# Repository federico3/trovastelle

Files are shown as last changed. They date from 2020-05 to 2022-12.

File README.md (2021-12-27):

# Il Trovastelle

Il Trovastelle punta a oggetti interessanti nel cielo e sulla Terra. Sa dove trovare pianeti, lune, e asteroidi, missioni spaziali e satelliti, galassie e nebulose, e amici vicini e lontani.

Il Trovastelle (https://www.youtube.com/watch?v=bgFfTYJVfwA)

## Come funziona

Il Trovastelle usa un accelerometro, una bussola, un giroscopio, e un orologio molto preciso per sapere dove trovare oggetti nel cielo.

[Ecco un video del Trovastelle dall'accensione alle operazioni.]( https://youtu.be/bmjY_7tN_tI )

## Configurazione

Per iniziare, collega un alimentatore da 12V[^1] con jack da 2.1mm (pin centrale positivo) al Trovastelle, e premi il pulsante di accensione.

### Connetti il Trovastelle a Internet

Il Trovastelle funziona senza alcuna connessione a Internet; tuttavia, con una connessione a Internet, può trovare anche satelliti nel cielo (per esempio, Hubble e la ISS).

Per collegare il Trovastelle a Internet, cerca una connessione WiFi aperta dal nome `comitup-XXX`.

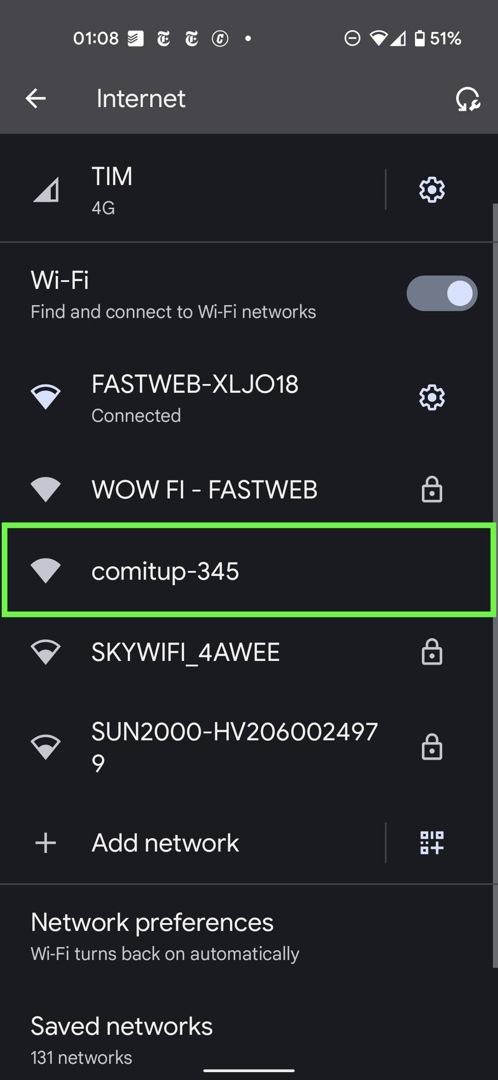
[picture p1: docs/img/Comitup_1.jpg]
Look for an open WiFi network named comitup-XXX


Collegati alla rete WiFi `comitup`. Il tuo computer o telefono aprirà una finestra pop-up che ti chiede di scegliere la tua rete WiFi.

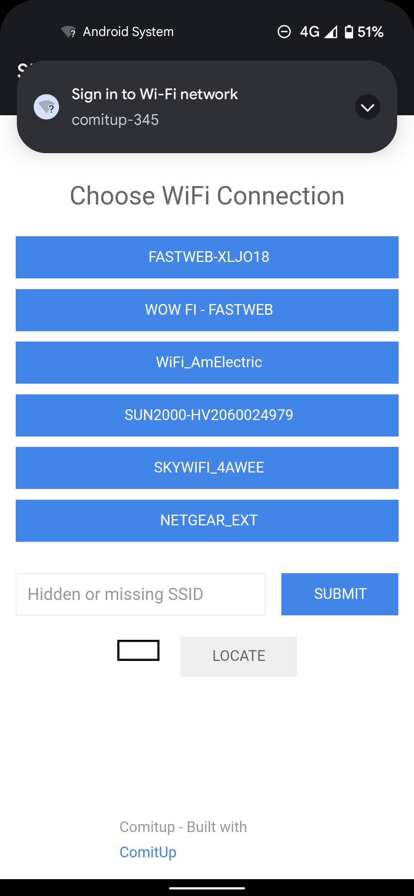
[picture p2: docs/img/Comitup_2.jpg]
Select your WiFi network


Scegli la tua rete WiFi e inserisci la password. Il Trovastelle farà sparire la rete `comitup` e si collegherà al tuo WiFi.

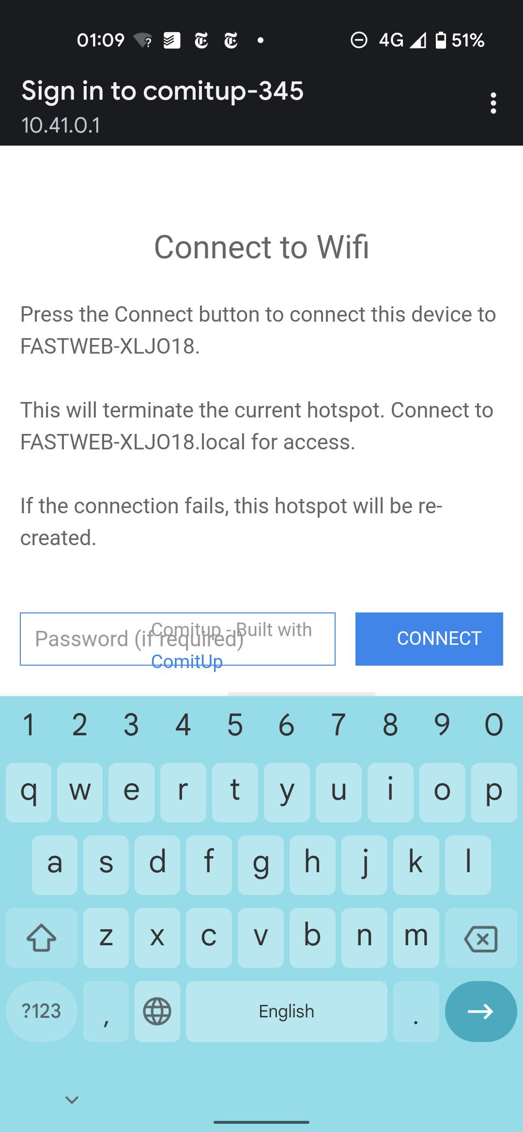
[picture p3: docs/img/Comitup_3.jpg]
Input your WiFi password


### Accedi al Trovastelle

Il cuore del Trovastelle è un computer Raspberry Pi con Linux. Una volta connesso il Trovastelle alla rete WiFi di casa, puoi collegarti al computer via ssh se hai le chiavi giuste:

```
ssh pi@trovastelle1.local
```

Questo comando funzionerà solamente se (i) sei sulla stessa rete WiFi del Trovastelle, e (ii) hai una chiave privata SSH corrispondente alla chiave pubblica caricata sul Trovastelle.

### Telemetria

Il Trovastelle può collegarsi al server di Federico per ricevere aggiornamenti (forse) e aiutare il debug di eventuali problemi. Questa impostazione è disattivata di default. Per attivarla, collegati al Trovastelle via SSH e usa questo comando:
```
sudo systemctl enable autossh
sudo systemctl start autossh
```
Per disattivare questa impostazione, usa questo comando:
```
sudo systemctl stop autossh
sudo systemctl disable autossh
```
Quando la telemetria è attiva, Federico può collegarsi via ssh al Trovastelle, cambiare il programma caricato a bordo, vedere le misure prese dall'accelerometro, giroscopio, e bussola, e comandare i motori, il display, e il LED.

### Progetto meccanico

Il progetto Fusion 360 è [qui](https://a360.co/3moek6k).

[^1]: I motori hanno un voltaggio nominale di 9 e 12V, e dovrebbero funzionare con qualunque voltaggio tra 9 e 18V. Il computer di bordo tollera tra 6 e 21V. Le prove sono state fatte solo a 12V.
  Il Trovastelle non consuma molto: 1A a 12V dovrebbe essere ben più che sufficiente.

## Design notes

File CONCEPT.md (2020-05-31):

# Sky Finder

An arrow that points at interesting objects in the sky, inspired by the art installation at the JPL mall.

## Basic idea

A pointing mechanism (an arrow and/or a laser pointer) that will point out interesting targets in the sky either automatically or in response to user input.

Targets may include

- Stars, galaxies, and other interesting deep sky objects
- Earth satellites
- Locations on Earth (mountains, cities, friends)
- Airplanes?

The mechanism should have a screen to display what is being observed.

## Hardware

### Frame and Assembly

### Motors

Steppers, servos, simple DC motors?

Need a motor driver

### Display

### Laser Pointer

### Brains

System-on-a-chip (SoC) like a Raspberry Pi or microcontroller like ESP/Arduino?

- SoC is way easier to work with (existing astronomy libraries, etc) and has no storage/RAM limitations, but boots slowly and has higher power consumption.
- Microcontroller boots instantly and has lower power usage, but is _very_ limited (a few kBs of RAM).

### Power

USB plug and built-in battery? Need a charge controller to automatically switch from shore power to on-board battery.

## Design concepts

### V1: Sky only, semi-automatic

A pair of stepper motors actuate the pointing mechanism. A microcontroller keeps track of the location of the stepper motors and reports it to SkySafari through the [basic encoder protocol](https://github.com/federico3/DobsonianDSC). [SkySafari](https://play.google.com/store/apps/details?id=com.simulationcurriculum.skysafari5&hl=en_US) issues GOTO commands to the microcontroller via the same protocol. All projections and translations from steps to sky coordinates are performed by Sky Safari.

> TODO: does SkySafari send GoTo commands with the basic protocol?

No screen, no laser pointer, no way to automatically point at objects, calibration needed before every use.

Downside: needs external calibration before use.

### V2: self-calibrating

A compass and accelerometer are installed on the pointing mechanism. This way, the arrow knows where it is pointed (to a precision of a few degrees) in the local alt-az frame. The arrow can communicate its azm-alt to Sky Safari using the [NexStar serial protocol](https://s3.amazonaws.com/celestron-site-support-files/support_files/1154108406_nexstarcommprot.pdf). Conversions from ra-dec to alt-az can be handled with, e.g., [astropy](https://gist.github.com/dokeeffe/18857db66dbabc14679c20a8560e2cd6). 

#### Software updates

- SkySafari compatibility with new protocol
- Cycle through scripted celestial objects autonomously
- Slew to follow satellites autonomously
- Cycle through ground-based objects (lon-lat) autonomously
- Read airplane locations from fr24 or adsbexchange 

#### V2.1: display

V2, but with a display to show what the arrow is pointing at.

#### V2.2: GPS

Automatically get time and location from a GPS receiver.

#### V3.0: laser

V2, but with a laser to point to interesting objects. The laser is controlled by the microcontroller and there is a safety interlock on the base, requiring the user to be present for use.

#### V4.0: camera and astrometry.net

To increase precision, the arrow incorporates a camera that looks at the sky and plate-solves. Probably _very_ unnecessary and may make things more complicated if plate-solving is used by day.

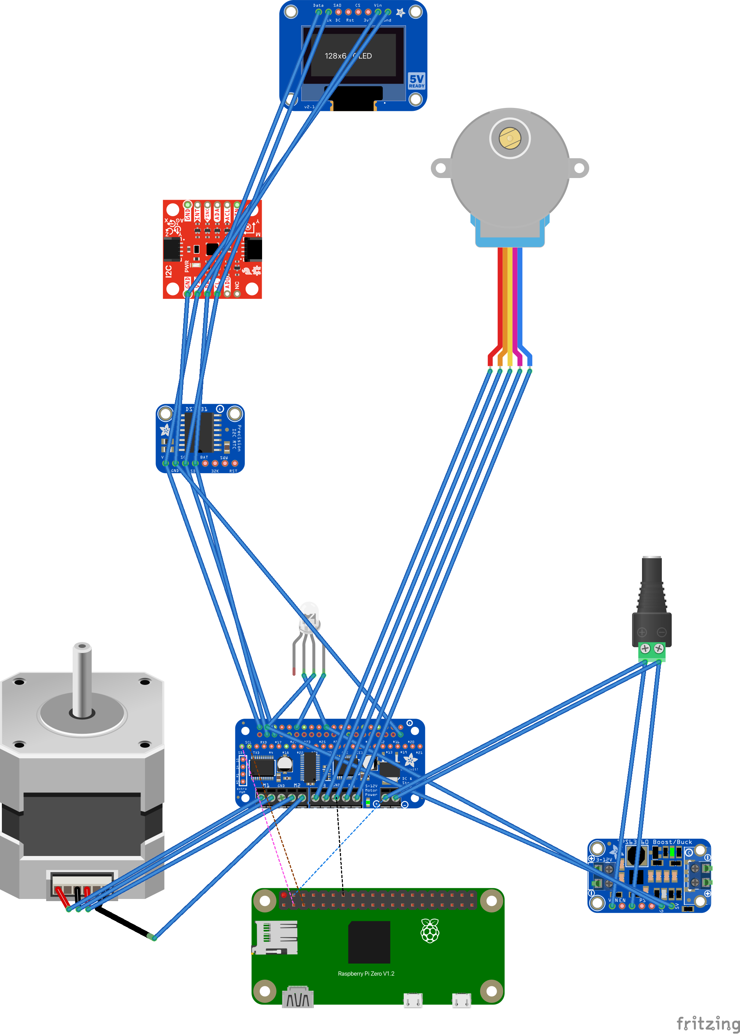
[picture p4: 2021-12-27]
electrical/arrow_bb.png

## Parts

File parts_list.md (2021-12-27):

# Trovastelle

## Hardware

### Computer

- [X] Raspy 0W: $14 https://www.adafruit.com/product/3708

### Motors

- [X] Stepper motors: https://www.adafruit.com/product/858
- [X] https://www.pololu.com/product/1207 16+5

- [X] Motor controller or https://www.adafruit.com/product/4280 (Pi) +22

### Sensors

- [X] Accelerometer+compass: https://www.sparkfun.com/products/15335 $16 or https://www.adafruit.com/product/4646 ($20)

~~GPS: https://www.adafruit.com/product/4415~~

~~QT hat: https://www.adafruit.com/product/4688~~

- [X] RTC https://www.adafruit.com/product/5188 (best) or https://www.adafruit.com/product/5189
- [X] RTC coin cell

### Display

~~Display: https://www.adafruit.com/product/2232 (overkill) or https://www.adafruit.com/product/4567 (monochrome, pretty!) or https://www.adafruit.com/product/2097 (Pi) or https://www.adafruit.com/product/2298 or https://www.aliexpress.com/item/1005003093058462.html~~

- [X] Display: https://www.aliexpress.com/item/1005003093058462.html ($14)

### Other hardware

- [X] Slip ring: https://www.adafruit.com/product/1196 ($20)

- [X] Stepper motor collar: https://www.pololu.com/product/1998 + https://www.pololu.com/product/2693 $7.5+8

- [X] DC barrel: https://www.adafruit.com/product/610 $3

- [X] 12V to 5V buck: https://www.adafruit.com/product/4739 $6

- [X] Power supply: https://www.adafruit.com/product/798 $15

LED may be nice: https://www.sparkfun.com/products/12877 or https://www.sparkfun.com/products/12986

- [X] Power button (AliExpress)

- [X] QWIIC adapter: https://www.adafruit.com/product/4463 or https://www.sparkfun.com/products/15794 or https://www.adafruit.com/product/5142

#### Connectors

- [ ] Connectors: 
  - [X] JST PH connector for motor https://www.adafruit.com/product/5089
  - [X] 2X QWIIC cables https://www.adafruit.com/product/4401
  - [X] 1X QWIIC cable https://www.adafruit.com/product/4399
  - [X] 2X Riser pins https://www.adafruit.com/product/2223
  - [X] Angled riser pins https://www.adafruit.com/product/2823
  - [X] Arcade quick release: https://www.adafruit.com/product/1152
  - [X] Plug jumpers https://www.adafruit.com/product/758
  - [X] Socket jumpers https://www.adafruit.com/product/266
  - [X] Heat shrink https://www.adafruit.com/product/4559

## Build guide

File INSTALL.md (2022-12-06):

# Installation

## Backend

To install the backend, add `trovastelle.service` as a systemd service.

1. Install the Python requirements for Trovastelle with `python -m pip install -r requirements.txt` in the root folder of this repo.
1. Install the package with `python -m pip install -e .` in the root folder of this repo. Note that `-e` symlinks the package to the current folder instead of copying, which is a good idea for development.
1. Ensure that the paths in `trovastelle.service` and `trovastelle.sh` in the `/src/celestial-compass/` folder match the path where this folder is.
1. Copy `trovastelle.service` in the `/src/celestial-compass/` folder to /`etc/systemd/system`.
1. Run `systemctl enable trovastelle`
1. Run `systemctl start trovastelle`

## Frontend

To install the frontend:

1. Copy `trovastelle.wsgi` in the ``/src/celestial-compass/` folder to `/var/www/wsgi-scripts`.
1. Create a file `trovastelle_web.log` in `/var/www/wsgi-scripts` and ensure that it is owned by the `pi` user: `cd /var/www/wsgi-scripts && sudo touch trovastelle_web.log && sudo chown pi trovastelle_web.log`.
1. Compile the frontend with `npm run build` in the `frontend` folder.
1. Copy the frontend installation files in `frontend/build` to `/var/www/frontend`.
1. Ensure that Apache and mod_wsgi are installed.
1. Copy `020-wsgi-backend.conf` to `/etc/apache2/sites-available`. 
1. Run `sudo a2enmod 020-wsgi-backend.conf`.
1. Restart the Apache2 daemon with `sudo systemctl reload apache2`.

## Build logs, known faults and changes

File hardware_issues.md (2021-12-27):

# Problemi hardware

- [ ] Il pin del LED verde è staccato
- [ ] Il riduttore a ingranaggi per l'asse azimuth è rumorosissimo; probabilmente un riduttore a cinghia sarebbe meglio?
- [ ] Il Trovastelle è letteralmente tenuto insieme con lo scotch
- [ ] I cavi sono tenuti in posizione con lo scotch
- [ ] Il magnetometro è molto vicino al motore di elevation, che introduce un sacco di rumore nella misurazione
- [ ] Lo schermo si vede solamente da un lato della freccia
- [ ] Il chip RTC è messo in un posto a caso (con lo scotch) per rendere sufficientemente lungo il cavo che porta segnali alla freccia
- [ ] Le saldature dei cavi sono da software engineer

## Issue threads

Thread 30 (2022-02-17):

Revise Az tracking

federico3, 2022-02-17:
Turns out laser-cut gears are super noisy and inefficient. Consider commercial alternatives.

Also consider making the position of the stepper something we can calibrate.

Options:

- Gears: ~$20
  - [Stepper](https://www.servocity.com/mod-0-8-pitch-pinion-gears/#bore-5mm-round) ($8.5). Can also get more teeth on [eBay](https://www.ebay.com/sch/i.html?_from=R40&_trksid=p2380057.m570.l1313&_nkw=MOD+0.8+5mm&_sacat=0).
  - [Arrow base](https://www.servocity.com/64-tooth-hub-mount-gear-mod-0-8-4mm-thick-acetal/) (number of gears negotiable, $3.5. Can also go aluminum for $10)
  - [Arrow base hub](https://www.servocity.com/1310-series-hyper-hub-8mm-bore/) ($6)
- Timing belts
  - XL $30+8
    - [Stepper](https://www.servocity.com/5mm-15-tooth-pinion-pulley/) $7.6
    - [Arrow base](https://www.servocity.com/timing-hub-pulley/) $6.8
    - [Hub adapter](https://www.servocity.com/1-50-0-770-pattern-adapter/) $4.5
    - [Hub 8mm](https://www.servocity.com/8mm-0-770-clamping-hub/) $6
    - [Belt](https://www.servocity.com/all-xl-series-3-8-width-timing-belts/) $4
  - 3mm ~$26+8
    - [Stepper](https://www.servocity.com/3402-series-3mm-htd-pitch-plastic-hub-mount-timing-belt-pulley-14mm-bore-36-tooth/) $3.4
    - [Stepper hub](https://www.servocity.com/1308-series-lightweight-set-screw-hub-5mm-bore/) $4.7
    - [Arrow base](https://www.servocity.com/3402-series-3mm-htd-pitch-plastic-hub-mount-timing-belt-pulley-14mm-bore-108-tooth/) $6.8
    - [Arrow base hub](https://www.servocity.com/1310-series-hyper-hub-8mm-bore/) ($6)
    - [Timing belt](https://www.servocity.com/3mm-htd-timing-belts/) $5-10
    - [Tensioner bracket](https://www.servocity.com/1524-series-arc-slot-tensioner-bracket/) $5.1
    - [Idler](https://www.servocity.com/acetal-timing-belt-idler-6mm-id-x-12mm-od-18mm-width-1-2-2-pack/) $2.5
- O-ring belt $22+8
  - [Stepper](https://www.servocity.com/3401-series-set-screw-round-belt-pulley-5mm-bore-16mm-pd/) $3.4
  - [Arrow base](https://www.servocity.com/3400-series-hub-mount-round-belt-pulley-14mm-bore-64mm-pd/) $6
  - [Arrow base hub](https://www.servocity.com/1310-series-hyper-hub-8mm-bore/) $6
  - [Tensioner bracket](https://www.servocity.com/1524-series-arc-slot-tensioner-bracket/) $5.1
  - [Idler](https://www.servocity.com/acetal-timing-belt-idler-6mm-id-x-12mm-od-18mm-width-1-2-2-pack/) $2.5 OR [alternative](https://www.servocity.com/1607-series-idler-bearing-6mm-id-x-15mm-od-41mm-length/) $6
  - [Belt](https://www.servocity.com/metric-round-belts-pulleys/#round-belts) $6

A [thinner 8mm hub](https://www.servocity.com/1309-series-sonic-hub-8mm-bore/) (currently sold out).

federico3, 2022-02-17:
Pros and cons.

*Gears*
PRO: cheapest, stiffest.
CON: least efficient, requires precise placement, potentially loud.

*Timing belts*
PROS: more precise than O-ring. Easier to regulate than gears
CON: most expensive, vertical clearance, least reduction (2:1).

*O-ring*
PROS: mid-cost solution, easy to regulate.
CON: potentially slips.

federico3, 2022-04-04:
Progress! https://a360.co/3uOJDeg

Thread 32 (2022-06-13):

Hardware fixes

federico3, 2022-06-13:
- Add a few millimeters to base height
- Move holes for 9DOF a little bit
- Make slightly more room for switch plug and for RPi wiring

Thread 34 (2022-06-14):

Track planes

federico3, 2022-06-14:

federico3, 2022-06-14:
https://openskynetwork.github.io/opensky-api/python.html

federico3, 2022-12-07:
- Build a box around the observer
- Fetch the planes in the box
- Pick the closest one
- Create an Observable that queries the API every 10s and returns lat, lon, alt, similar to Mellyn
- Let skyfiels do the rest
- It the plane is no longer available, pick another one?
- If there are no available planes, delete yourself and call a schedule repair?

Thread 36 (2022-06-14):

Relax calibration

federico3, 2022-06-14:
Adafruit says that, so long as the system calibration level is 1 or higher, we will have North. We can perhaps relax this check to system calibration>=1, or >=2.

https://github.com/federico3/trovastelle/blob/728f7747b047c4d5ffe4e4ecb46975634a518b4d/src/celestial_compass/arrow_controller.py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

federico3, 2022-06-14:
```print(bno055.calibration_status)  #Tuple containing sys, gyro, accel, and mag calibration data```
Just check that sys>=2, or that all are >=2.

federico3, 2022-10-30:
Resolved in #40

Closed 2022-10-30.

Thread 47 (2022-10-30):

Allow user to manually commit updates.

federico3, 2022-10-30:
Right now any update automatically reflects in the application. This also causes the config to get overwritten whenever the page is opened, which is less than great. Fix: add a button to upload configuration, remove autoupload.

Closed 2022-12-04.

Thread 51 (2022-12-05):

Intermittent i2c error in trovastelle2

federico3, 2022-12-05:
Often, trovastelle2 will give this error:

```
➜ python trovastelle.py
Traceback (most recent call last):
  File "/home/pi/trovastelle/src/celestial_compass/trovastelle.py", line 438, in <module>
    asyncio.run(ts.run(),debug=_debug)
  File "/usr/lib/python3.9/asyncio/runners.py", line 44, in run
    return loop.run_until_complete(main)
  File "/usr/lib/python3.9/asyncio/base_events.py", line 642, in run_until_complete
    return future.result()
  File "/home/pi/trovastelle/src/celestial_compass/trovastelle.py", line 399, in run
    await cc_task
  File "/home/pi/trovastelle/src/celestial_compass/compass.py", line 168, in run
    await main_task
  File "/home/pi/trovastelle/src/celestial_compass/compass.py", line 233, in _run_main
    self.display_controller.display_observable_data(
  File "/home/pi/trovastelle/src/celestial_compass/display_manager.py", line 241, in display_observable_data
    self._display_text_in_box(
  File "/home/pi/.local/lib/python3.9/site-packages/luma/core/render.py", line 43, in __exit__
    self.device.display(self.image)
  File "/home/pi/.local/lib/python3.9/site-packages/luma/oled/device/__init__.py", line 225, in display
    self.data(list(buf))
  File "/home/pi/.local/lib/python3.9/site-packages/luma/core/device.py", line 55, in data
    self._serial_interface.data(data)
  File "/home/pi/.local/lib/python3.9/site-packages/luma/core/interface/serial.py", line 125, in data
    write(list(data[i:i + block_size]))
  File "/home/pi/.local/lib/python3.9/site-packages/luma/core/interface/serial.py", line 134, in _write_large_block
    self._bus.i2c_rdwr(self._i2c_msg_write(self._addr, [self._data_mode] + data))
  File "/home/pi/.local/lib/python3.9/site-packages/smbus2/smbus2.py", line 658, in i2c_rdwr
    ioctl(self.fd, I2C_RDWR, ioctl_data)
OSError: [Errno 121] Remote I/O error
```

Looks like this is an i2c error. It may have to do with the clock not being properly stretched, or just some issue with how the display is wired (remember that terrible soldering job?), or just noise. When this happens, the whole application crashes and does not restart.

Closed 2022-12-06.

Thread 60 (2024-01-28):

Add a try-catch for display update

federico3, 2024-01-28:
App keeps crashing while updating the display due to a finicky i2c bus. Ok, it's an hardware issue, but it's annoying.

```
Jan 28 11:40:14 trovastelle2 systemd[1]: Started Trovastelle service.
Jan 28 11:43:54 trovastelle2 trovastelle.sh[4122]: Slow display update prop is False
Jan 28 11:43:54 trovastelle2 trovastelle.sh[4122]: Traceback (most recent call last):
Jan 28 11:43:54 trovastelle2 trovastelle.sh[4122]:   File "/home/pi/trovastelle/src/celestial_compass/trovastelle.py", line 451, in <module>
Jan 28 11:43:54 trovastelle2 trovastelle.sh[4122]:     asyncio.run(ts.run(),debug=_debug)
Jan 28 11:43:54 trovastelle2 trovastelle.sh[4122]:   File "/usr/lib/python3.9/asyncio/runners.py", line 44, in run
Jan 28 11:43:54 trovastelle2 trovastelle.sh[4122]:     return loop.run_until_complete(main)
Jan 28 11:43:54 trovastelle2 trovastelle.sh[4122]:   File "/usr/lib/python3.9/asyncio/base_events.py", line 642, in run_until_complete
Jan 28 11:43:54 trovastelle2 trovastelle.sh[4122]:     return future.result()
Jan 28 11:43:54 trovastelle2 trovastelle.sh[4122]:   File "/home/pi/trovastelle/src/celestial_compass/trovastelle.py", line 412, in run
Jan 28 11:43:54 trovastelle2 trovastelle.sh[4122]:     await cc_task
Jan 28 11:43:54 trovastelle2 trovastelle.sh[4122]:   File "/home/pi/trovastelle/src/celestial_compass/compass.py", line 174, in run
Jan 28 11:43:54 trovastelle2 trovastelle.sh[4122]:     await main_task
Jan 28 11:43:54 trovastelle2 trovastelle.sh[4122]:   File "/home/pi/trovastelle/src/celestial_compass/compass.py", line 239, in _run_main
Jan 28 11:43:54 trovastelle2 trovastelle.sh[4122]:     self.display_controller.display_observable_data(
Jan 28 11:43:54 trovastelle2 trovastelle.sh[4122]:   File "/home/pi/trovastelle/src/celestial_compass/display_manager.py", line 269, in display_o>
Jan 28 11:43:54 trovastelle2 trovastelle.sh[4122]:     self._display_text_in_box(
Jan 28 11:43:54 trovastelle2 trovastelle.sh[4122]:   File "/home/pi/.local/lib/python3.9/site-packages/luma/core/render.py", line 43, in __exit__
Jan 28 11:43:54 trovastelle2 trovastelle.sh[4122]:     self.device.display(self.image)
Jan 28 11:43:54 trovastelle2 trovastelle.sh[4122]:   File "/home/pi/.local/lib/python3.9/site-packages/luma/oled/device/__init__.py", line 225, i>
Jan 28 11:43:54 trovastelle2 trovastelle.sh[4122]:     self.data(list(buf))
Jan 28 11:43:54 trovastelle2 trovastelle.sh[4122]:   File "/home/pi/.local/lib/python3.9/site-packages/luma/core/device.py", line 55, in data
Jan 28 11:43:54 trovastelle2 trovastelle.sh[4122]:     self._serial_interface.data(data)
Jan 28 11:43:54 trovastelle2 trovastelle.sh[4122]:   File "/home/pi/.local/lib/python3.9/site-packages/luma/core/interface/serial.py", line 125, >
Jan 28 11:43:54 trovastelle2 trovastelle.sh[4122]:     write(list(data[i:i + block_size]))
Jan 28 11:43:54 trovastelle2 trovastelle.sh[4122]:   File "/home/pi/.local/lib/python3.9/site-packages/luma/core/interface/serial.py", line 134, >
Jan 28 11:43:54 trovastelle2 trovastelle.sh[4122]:     self._bus.i2c_rdwr(self._i2c_msg_write(self._addr, [self._data_mode] + data))
Jan 28 11:43:54 trovastelle2 trovastelle.sh[4122]:   File "/home/pi/.local/lib/python3.9/site-packages/smbus2/smbus2.py", line 658, in i2c_rdwr
Jan 28 11:43:54 trovastelle2 trovastelle.sh[4122]:     ioctl(self.fd, I2C_RDWR, ioctl_data)
Jan 28 11:43:54 trovastelle2 trovastelle.sh[4122]: OSError: [Errno 121] Remote I/O error
```

federico3, 2024-02-03:
Actually we have already done that but OSError is not caught...

federico3, 2024-02-03:
https://www.geeksforgeeks.org/handling-oserror-exception-in-python/

https://stackoverflow.com/questions/63444603/catch-a-specific-oserror-exception-in-python-3

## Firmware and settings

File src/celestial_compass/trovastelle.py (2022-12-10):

"""
 Copyright (C) 2021 Federico Rossi (347N)
 
 This file is part of Trovastelle.
 
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

from turtle import color
from celestial_compass.display_manager import DisplayController, round_number_to_fixed_width, format_distance, test_distance_format
from celestial_compass.visibility_window import VisibilityWindow
import matplotlib.colors as mcolors
from celestial_compass.arrow_controller import ArrowController, sim9dof, simstepper 
import logging


from celestial_compass.compass import CelestialCompass
from celestial_compass.observables import ObserverLLA

import numpy as np
import os, json
import asyncio
import zmq
import zmq.asyncio
from geojson import Feature, Point, LineString


def get_observables(
    satellites: bool=True,
    missions: bool=True,
    planets: bool=True,
    smallbodies: bool=False,
    mellyn: bool=True,
    messiers: bool=True,
):
    # Observables config
    SPICEYPY_AVAILABLE = False
    try:
        import spiceypy as spice
        SPICEYPY_AVAILABLE = True
    except:
        logging.warning("Spiceypy is not available!")

    from celestial_compass.data.satellites import ObservableSatellites
    if SPICEYPY_AVAILABLE:
        from celestial_compass.data.missions import ObservableMissions
    else:
        from celestial_compass.data.missions_base import ObservableMissions
    from celestial_compass.data.planets import ObservablePlanets
    from celestial_compass.data.small_bodies import ObservableSmallBodies
    from celestial_compass.data.mellyn import ObservableMellyn    
    from celestial_compass.data.messier import ObservableMessiers

    Observables = []
    if satellites:
        Observables += ObservableSatellites
    if missions:
        Observables += ObservableMissions
    if planets:
        Observables += ObservablePlanets
    if smallbodies:
        Observables += ObservableSmallBodies
    if mellyn:
        Observables += ObservableMellyn
    if messiers:
        Observables += ObservableMessiers
    
    return Observables

class trovastelle(object):
    def __init__(self, config, color_schema, store_config=lambda x: None):
    # LED config
        self.config = config
        self.color_schema = color_schema
        logging.debug("Configuring LEDs")
        R_LED = config.get("led_pins",{}).get("red",5)
        G_LED = config.get("led_pins",{}).get("green",6)
        B_LED = config.get("led_pins",{}).get("blue",13)
        A_LED = config.get("led_pins",{}).get("alpha",19)
        led_anode_high = config.get("led_pins",{}).get("anode_high", False)
        led_voltage_scale = config.get("led_pins",{}).get("voltage_scale", 1.)

        self.store_config = store_config

        self.strong_colors_by_type = {
            'Mellon': "xkcd:hot green",
            'Messier': "xkcd:bright orange",
            'Mission': "xkcd:bright red",
            'Planet': "xkcd:true blue",
            'Satellite': "xkcd:very light purple",
        }

        # pale_colors_by_type = {
        #     'Mellon': "xkcd:pale",
        #     'Messier': "xkcd:baby green",
        #     'Mission': "xkcd:light periwinkle",
        #     'Planet': "xkcd:pale mauve",
        #     'Satellite': "xkcd:magenta",
        # }

        logging.debug("Configuring display")
        simulated_display = config.get("simulated",{}).get("display",False)
        if simulated_display:
            import luma.emulator.device
            device = luma.emulator.device.capture()
            display_controller = DisplayController(device=device, slow_display_update=config.get("slow_display_update", True))
            logging.info("Using simulated display in trovastelle")
        else:
            display_controller = DisplayController(slow_display_update=config.get("slow_display_update", True))
            logging.info("Using real display in trovastelle")
        display_controller.display_fullscreen_text("Trovastelle")


        logging.debug("Configuring observables")
        Observables = get_observables(
            satellites  = config.get("observables",{}).get("satellites",True),
            missions    = config.get("observables",{}).get("missions",True),
            planets     = config.get("observables",{}).get("planets",True),
            smallbodies = config.get("observables",{}).get("smallbodies",False),
            mellyn      = config.get("observables",{}).get("mellyn",True),
            messiers    = config.get("observables",{}).get("messiers",True),
        )

        logging.debug("Configuring observer")
        # Observer: Marzia
        # _observer = ObservableMellyn[4]

        observer = ObserverLLA(
            lat_rad = config.get("observer",{}).get("lat_deg_N", 34.1376481)*np.pi/180.,
            lon_rad = config.get("observer",{}).get("lon_deg_E",-118.138686)*np.pi/180.,
            alt_m   = config.get("observer",{}).get("alt_m", 204.),
        )

        logging.debug("Configuring arrow controller")
        # Arrow controller
        ac = ArrowController(
            simulate_motors=config.get("simulated",{}).get("motors",False),
            simulate_9dof=config.get("simulated",{}).get("9dof",False),
            steps_per_turn_alt=config.get("steppers",{}).get("steps_per_turn_alt",2052),
            steps_per_turn_az=config.get("steppers",{}).get("steps_per_turn_az",int(200*16/6)),
            az_offset_rad=-np.pi/2, # HORRIBLE HACK! But works on Federico's desk, and YOLO
            alt_direction_up = config.get("steppers",{}).get("alt_direction_up", 2) , # 1 is forward, 2 is backwards
            az_direction_cw = config.get("steppers",{}).get("az_direction_cw", 2) ,
        )

        logging.debug("Configuring Trovastelle")
        # Full controller
        self.cc = CelestialCompass(
                controller= ac,
                observer = observer,
                observables = Observables,
                time_on_target_s = config.get("observables_list",{}).get("time_on_target_s",150.),
                target_list_length_s = config.get("observables_list",{}).get("target_list_length_s",600.),
                check_visible= config.get("observables_list",{}).get("check_visible",False),
                visibility_window = VisibilityWindow(
                    min_alt_rad= config.get("observables_list",{}).get("visibility_window",{}).get("min_alt_rad",-np.pi/2.),
                    max_alt_rad= config.get("observables_list",{}).get("visibility_window",{}).get("max_alt_rad", np.pi/2.),
                    min_az_rad = config.get("observables_list",{}).get("visibility_window",{}).get("min_az_rad",  0.),
                    max_az_rad = config.get("observables_list",{}).get("visibility_window",{}).get("max_az_rad",2*np.pi),
                ),
                refresh_rate_hz=config.get("observables_list",{}).get("refresh_rate_hz",1.),
                display_controller=display_controller,
                simulated_display=config.get("simulated",{}).get("display",False),
                simulated_led=config.get("simulated",{}).get("led",False),
                led_pins_rgba = (R_LED, G_LED, B_LED, A_LED),
                led_anode_high = led_anode_high,
                led_voltage_scale = led_voltage_scale,
                led_colors=color_schema.get(config.get("led_color_scheme","strong"), self.strong_colors_by_type),
                calibration_level=config.get("calibration_level",3),
                slow_display_update=config.get("slow_display_update", True),
            )


    def calibrate(self):
        logging.info("Calibrating! Trovastelle")
    
        self.cc.calibrate()

    async def listen(self):
        """ This is where you put your sockets, etc. """
        """ https://pyzmq.readthedocs.io/en/latest/api/zmq.asyncio.html """
        context = zmq.asyncio.Context()
        sock = context.socket(zmq.REP)
        sock.bind("tcp://*:5556")
        while True:
            msg = await sock.recv() # waits for msg to be ready
            req = msg.decode()
            if len(req) == 2 and req[:2] == "GC":
                logging.debug("Received request for config")
                reply = json.dumps(self.config)

            elif len(req) == 2 and req[:2] == "GA":
                logging.debug("Received request for calibration status")
                reply = json.dumps(self.cc.controller.calibration_status)
            
            elif len(req) == 2 and req[:2] == "GO":
                logging.debug("Received request for observer location status")
                reply = json.dumps({"lat_deg_N": self.cc.observer.lat_rad*180./np.pi, "lon_deg_E": self.cc.observer.lon_rad*180./np.pi, "alt_m": self.cc.observer.alt_m})
            
            elif len(req) == 2 and req[:2] == "GL":
                logging.debug("Received request for list")
                _schedule_json = []
                for scheduled_ix, scheduled in enumerate(self.cc.schedule):
                    _ra_radians_start, _dec_radians_start, _distance = scheduled['observable'].observe_topocentric_ra_dec(
                        observer_lon_E_deg=self.cc.observer.lon_rad*180./np.pi,
                        observer_lat_N_deg=self.cc.observer.lat_rad*180./np.pi,
                        observer_h_m=self.cc.observer.alt_m,
                        observing_time=scheduled['start_time']
                        )
                    _ra_radians_end, _dec_radians_end, _distance = scheduled['observable'].observe_topocentric_ra_dec(
                        observer_lon_E_deg=self.cc.observer.lon_rad*180./np.pi,
                        observer_lat_N_deg=self.cc.observer.lat_rad*180./np.pi,
                        observer_h_m=self.cc.observer.alt_m,
                        observing_time=scheduled['end_time']
                        )
                    # if (_ra_radians_start==_ra_radians_end and _dec_radians_start==_dec_radians_end):
                    if True:
                        _geometry = Point((
                                _ra_radians_start*180/np.pi,
                                _dec_radians_start*180/np.pi
                            ))
                    else:
                        _geometry = LineString([
                            (_ra_radians_start*180/np.pi,_dec_radians_start*180/np.pi),
                            (_ra_radians_end*180/np.pi,  _dec_radians_end*180/np.pi)
                            ])
                    _schedule_json.append(
                        Feature(
                            properties={
                                "name": scheduled['observable'].name,
                                "type": scheduled['observable'].type_name,
                                "order": scheduled_ix, 
                                "start_time": scheduled['start_time'].strftime("%m/%d/%Y, %H:%M:%S"),
                                "end_time": scheduled['end_time'].strftime("%m/%d/%Y, %H:%M:%S"),
                                "color_rgb": scheduled['color_rgb']
                            },
                            geometry= _geometry
                        )
                    )

                reply = json.dumps({"type":"FeatureCollection","features": _schedule_json})
            
            elif len(req) == 2 and req[:2] == "GP":
                logging.debug("Received request for pointer location")
                _alt_rad, _az_rad = self.cc.controller.get_alt_az()
                reply = json.dumps({"alt_rad": _alt_rad, "az_rad": _az_rad})

            elif len(req) >=2 and req[:2] == "SC":
                _config = json.loads(req[2:])
                logging.info("Processing new dictionary!")
                # print(_config)
                # Dynamic update behavior:
                # - Update observer: update cc.observer, set cc.schedule = [], call cc.update_schedule()
                # - Update observables: set cc.schedule = [], call cc.update_schedule()
                # - Update LED pins: requires application reboot
                # - Update LED color scheme: set cc.schedule = [], call cc.update_schedule() (or we could just update the colors one by one)
                # - Update stepper settings: requires application reboot
                # - Update observables_list parameters: 
                #   - update cc.time_on_target_s | target_list_length_s | check_visible | visibility_window,  set cc.schedule = [], call cc.update_schedule()
                #   - update cc.refresh_rate_hz and continue running with existing
                # - Update simulated: requires application reboot
                _update_schedule = False
                _restart = False
                if "observables" in _config.keys() and _config["observables"] != self.config["observables"]:
                    logging.info("New observables")
                    logging.debug("Fetching new observables: {}".format(_config.get("observables",{})))
                    _Observables = get_observables(
                        satellites  = _config.get("observables",{}).get("satellites",True),
                        missions    = _config.get("observables",{}).get("missions",True),
                        planets     = _config.get("observables",{}).get("planets",True),
                        smallbodies = _config.get("observables",{}).get("smallbodies",False),
                        mellyn      = _config.get("observables",{}).get("mellyn",True),
                        messiers    = _config.get("observables",{}).get("messiers",True),
                    )
                    logging.debug("Fetched {} new observables".format(len(_Observables)))
                    # Very weird, this sometimes does not work. Some race condition?
                    _updated_observables = self.cc.update_observables(_Observables)
                    logging.debug("Updated observables: {}".format(_updated_observables))
                    # self.cc.observables = _Observables
                    _update_schedule = True
                    self.config["observables"] = _config["observables"]

                if "observer" in _config.keys() and _config["observer"] != self.config["observer"]:
                    logging.info("New observer")
                    self.cc.observer = ObserverLLA(
                        lat_rad = float(_config.get("observer",{}).get("lat_deg_N", 34.1376481)*np.pi/180.),
                        lon_rad = float(_config.get("observer",{}).get("lon_deg_E",-118.138686)*np.pi/180.),
                        alt_m   = float(_config.get("observer",{}).get("alt_m", 204.)),
                    )
                    _update_schedule = True
                    self.config["observer"] = _config["observer"]

                if "observables_list" in _config.keys() and _config["observables_list"] != self.config["observables_list"]:
                    logging.info("New observable list parameters")
                    self.cc.time_on_target_s = int(_config.get("observables_list",{}).get("time_on_target_s", 150))
                    self.cc.target_list_length_s = int(_config.get("observables_list",{}).get("target_list_length_s", 600))
                    self.cc.check_visible = _config.get("observables_list",{}).get("check_visible", True)
                    self.cc.visibility_window = VisibilityWindow(
                        min_alt_rad= float(_config.get("observables_list",{}).get("visibility_window",{}).get("min_alt_rad",-np.pi/2.)),
                        max_alt_rad= float(_config.get("observables_list",{}).get("visibility_window",{}).get("max_alt_rad", np.pi/2.)),
                        min_az_rad = float(_config.get("observables_list",{}).get("visibility_window",{}).get("min_az_rad",  0.)),
                        max_az_rad = float(_config.get("observables_list",{}).get("visibility_window",{}).get("max_az_rad",2*np.pi)),
                    )
                    self.cc.refresh_rate_hz = _config.get("observables_list",{}).get("refresh_rate_hz", 1.)
                    _update_schedule = True
                    self.config["observables_list"] = _config["observables_list"]

                if "calibration_level" in _config.keys() and _config["calibration_level"] != self.config["calibration_level"]:
                    logging.info("New calibration level - this will really take effect at the next restart")
                    self.cc.calibration_level = _config["calibration_level"] # This line is quite ineffective, actually. The important thing is that the setting gets saved to disk.
                    self.config["calibration_level"] = _config["calibration_level"]

                if "led_color_scheme" in _config.keys() and _config["led_color_scheme"] != self.config["led_color_scheme"]:
                    logging.info("New color scheme")
                    self.cc.led_colors = self.color_schema.get(_config.get("led_color_scheme","strong"), self.strong_colors_by_type),
                    _update_schedule = True
                    self.config["led_color_scheme"] = _config["led_color_scheme"]

                if "led_pins" in  _config.keys() and _config["led_pins"] != self.config["led_pins"]:
                    logging.info("New LED pins")
                    self.config["led_pins"] = _config["led_pins"]
                    _restart = True

                if "steppers" in  _config.keys() and _config["steppers"] != self.config["steppers"]:
                    logging.info("New stepper properties")
                    self.config["steppers"] = _config["steppers"]
                    _restart = True

                if "simulated" in  _config.keys() and _config["simulated"] != self.config["simulated"]:
                    logging.info("New simulation properties")
                    self.config["simulated"] = _config["simulated"]
                    _restart = True

                if "slow_display_update" in  _config.keys() and _config["slow_display_update"] != self.config["slow_display_update"]:
                    logging.info("New slow display update configuration: {}".format(_config["slow_display_update"]))
                    self.cc.display_controller.slow_display_update = _config["slow_display_update"]
                    self.config["slow_display_update"] = _config["slow_display_update"]
                
                # self.config = _config # We do this piecemeal
                # Store configuration on disk!
                self.store_config(self.config)

                if _update_schedule is True:
                    logging.info("Updating schedule")
                    self.cc.schedule = []
                    self.cc.update_schedule()
                if _restart is True:
                    logging.info("Restarting")
                    pass # TODO Raise an Exception or just quit and systemd will respawn us
                reply_code = "OK"
                reply = reply_code+json.dumps(self.config)
            elif len(req) >=2 and req[:2] == "SO":
                _new_observer = json.loads(req[2:])
                if (
                    type(_new_observer) is not dict or
                    "lon_deg_E" not in _new_observer.keys() or
                    "lat_deg_N" not in _new_observer.keys() or
                    "alt_m" not in _new_observer.keys() or
                    np.abs(_new_observer["lon_deg_E"])>180. or
                    np.abs(_new_observer["lat_deg_N"])>90.
                ):
                    logging.warning("New observer is invalid (SO)")
                    reply_code = "NO"
                else:
                    logging.debug("New observer is valid, processing")
                    if (
                        self.cc.observer.lat_rad != _new_observer["lat_deg_N"]*np.pi/180. or
                        self.cc.observer.lon_rad != _new_observer["lon_deg_E"]*np.pi/180. or
                        self.cc.observer.alt_m != _new_observer["alt_m"]
                    ):

                        self.cc.observer = ObserverLLA(
                            lat_rad = _new_observer["lat_deg_N"]*np.pi/180.,
                            lon_rad = _new_observer["lon_deg_E"]*np.pi/180.,
                            alt_m   = _new_observer["alt_m"],
                        )

                        self.config["observer"] = _new_observer
                        self.cc.schedule = []
                        self.cc.update_schedule()
                    else:
                        logging.debug("Observer has not changed")
                    reply_code = "OK"
                    
                # reply = await async_process(msg)
                reply = reply_code+json.dumps(self.config["observer"])

            elif len(req) >=2 and req[:2] == "DL":
                logging.info("Received request to delete and reset schedule list")
                self.cc.schedule = []
                self.cc.update_schedule()
                reply = "OK";
            else:
                reply = "NO";
            await sock.send(reply.encode())

    async def run(self):
        cc_task = asyncio.create_task(self.cc.run())
        io_task = asyncio.create_task(self.listen())
        await cc_task
        await io_task
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

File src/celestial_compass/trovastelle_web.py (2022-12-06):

"""
 Copyright (C) 2021 Federico Rossi (347N)
 
 This file is part of Trovastelle.
 
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
import logging
import os, json
import asyncio
import zmq
import zmq.asyncio
from flask import Flask, request

from flask_cors import CORS



REQUEST_TIMEOUT = 10000
REQUEST_RETRIES = 3
SERVER_ENDPOINT = "tcp://localhost:5556"
DATA_PATH = os.environ.get("CELESTIAL_COMPASS_DATA")

class trovastelle_web_stateless(object):
    def __init__(self, endpoint, timeout, retries):
        self.endpoint = endpoint
        self.timeout = timeout

    def get_configuration(self):
        command = 'GC'
        request = str(command).encode()
        logging.info("Sending (%s)", request)
        context = zmq.Context()
        client = context.socket(zmq.REQ)
        client.connect(self.endpoint)

        client.send(request)
        while True:
            if (client.poll(REQUEST_TIMEOUT) & zmq.POLLIN) != 0:
                reply = client.recv().decode()
                try:
                    config = json.loads(reply)
                    retries_left = REQUEST_RETRIES
                    logging.info("Server replied OK (%s)", reply)
                    return config
                except ValueError:                    
                    logging.error("Malformed reply from server (%s): %s", command[:2], reply)
                    return None

    def get_observer(self):
        command = 'GO'
        request = str(command).encode()
        logging.info("Sending (%s)", request)
        context = zmq.Context()
        client = context.socket(zmq.REQ)
        client.connect(self.endpoint)

        client.send(request)
        while True:
            if (client.poll(REQUEST_TIMEOUT) & zmq.POLLIN) != 0:
                reply = client.recv().decode()
                try:
                    config = json.loads(reply)
                    retries_left = REQUEST_RETRIES
                    logging.info("Server replied OK (%s)", reply)
                    return config
                except ValueError:                    
                    logging.error("Malformed reply from server (%s): %s", command[:2], reply)
                    return None

    def get_list(self):
        command = 'GL'
        request = str(command).encode()
        logging.info("Sending (%s)", request)
        context = zmq.Context()
        client = context.socket(zmq.REQ)
        client.connect(self.endpoint)

        client.send(request)
        while True:
            if (client.poll(REQUEST_TIMEOUT) & zmq.POLLIN) != 0:
                reply = client.recv().decode()
                try:
                    config = json.loads(reply)
                    retries_left = REQUEST_RETRIES
                    logging.info("Server replied OK (%s)", reply)
                    return config
                except ValueError:                    
                    logging.error("Malformed reply from server (%s): %s", command[:2], reply)
                    return None

    def delete_list(self):
        command = 'DL'
        request = str(command).encode()
        logging.info("Sending (%s)", request)
        context = zmq.Context()
        client = context.socket(zmq.REQ)
        client.connect(self.endpoint)

        client.send(request)
        while True:
            if (client.poll(REQUEST_TIMEOUT) & zmq.POLLIN) != 0:
                reply = client.recv().decode()
                if reply[:2] != "OK":
                    logging.warning("Warning: non-OK reply from Trovastelle")
                    return False
                else:
                    return True


    def get_calibration(self):
        command = 'GA'
        request = str(command).encode()
        logging.info("Sending (%s)", request)
        context = zmq.Context()
        client = context.socket(zmq.REQ)
        client.connect(self.endpoint)

        client.send(request)
        while True:
            if (client.poll(REQUEST_TIMEOUT) & zmq.POLLIN) != 0:
                reply = client.recv().decode()
                try:
                    config = json.loads(reply)
                    retries_left = REQUEST_RETRIES
                    logging.info("Server replied OK (%s)", reply)
                    return config
                except ValueError:                    
                    logging.error("Malformed reply from server (%s): %s", command[:2], reply)
                    return None

    def get_altaz(self):
        command = 'GP'
        request = str(command).encode()
        logging.info("Sending (%s)", request)
        context = zmq.Context()
        client = context.socket(zmq.REQ)
        client.connect(self.endpoint)

        client.send(request)
        while True:
            if (client.poll(REQUEST_TIMEOUT) & zmq.POLLIN) != 0:
                reply = client.recv().decode()
                try:
                    config = json.loads(reply)
                    retries_left = REQUEST_RETRIES
                    logging.info("Server replied OK (%s)", reply)
                    return config
                except ValueError:                    
                    logging.error("Malformed reply from server (%s): %s", command[:2], reply)
                    return None

    def set_configuration(self, config):
        command = "SC"+json.dumps(config)
        request = str(command).encode()
        logging.debug("Sending (%s)", request)
        context = zmq.Context()
        client = context.socket(zmq.REQ)
        client.connect(self.endpoint)

        client.send(request)
        while True:
            if (client.poll(REQUEST_TIMEOUT) & zmq.POLLIN) != 0:
                reply = client.recv().decode()
                if reply[:2] != "OK":
                    logging.warning("Warning: non-OK reply from Trovastelle")
                try:
                    logging.warning(reply[2:])
                    config = json.loads(reply[2:])
                    retries_left = REQUEST_RETRIES
                    logging.warning("Server replied (%s)", reply)
                    return config
                    
                except ValueError:                    
                    logging.error("Malformed reply from server (%s): %s", command[:2], reply)
                    continue

    def set_observer(self, config):
        command = "SO"+json.dumps(config)
        request = str(command).encode()
        logging.debug("Sending (%s)", request)
        context = zmq.Context()
        client = context.socket(zmq.REQ)
        client.connect(self.endpoint)
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

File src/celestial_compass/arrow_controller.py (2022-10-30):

"""
 Copyright (C) 2021 Federico Rossi (347N)
 
 This file is part of Trovastelle.
 
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
from celestial_compass.observables import ObserverLLA
import numpy as np
import time
import logging
from scipy.spatial.transform import Rotation

BOARD_AVAILABLE=False
try:
    import board
    import adafruit_bno055
    from adafruit_motorkit import MotorKit

    BOARD_AVAILABLE=True
except NotImplementedError as e:
    logging.warning("Not on hardware!")
    board = None

from adafruit_motor import stepper

import geomag
import math

class sim9dof(object):
    def __init__(self, euler: list=(0,0,0), quaternion: list=(1,0,0,0)):
        self.euler = euler
        self.quaternion = quaternion
        self.calibrated = True
        self.calibration_status = (3,3,3,3)
        
class simstepper(object):
    def __init__(self):
        self._step = 0
    def onestep(
        self,
        direction,
        style,
    ):
        self._step += 1*direction
        return self._step
    def release(self):
        return True

class ArrowController(object):
    """
    """
    def __init__(
        self,
        steps_per_turn_alt:int=2052,
        steps_per_turn_az:int=200,
        observer:ObserverLLA=ObserverLLA(
            lat_rad=45.*np.pi/180.,
            lon_rad=8.*np.pi/180.
        ),
        az_offset_rad: float=0,
        simulate_motors: bool=False,
        simulate_9dof: bool=False,
        alt_direction_up = stepper.BACKWARD,
        az_direction_cw = stepper.BACKWARD,
    ):
        self.alt_rad = None
        self.az_rad = None
        self.az_offset_rad = az_offset_rad
        self.steps_per_turn_alt = steps_per_turn_alt
        self.steps_per_turn_az = steps_per_turn_az
        self.observer = observer
        self.alt_direction_up = alt_direction_up
        self.az_direction_cw = az_direction_cw
        
        if simulate_9dof:
            self.bno055 = sim9dof()
        else:
            i2c = board.I2C()
            self.bno055 = adafruit_bno055.BNO055_I2C(i2c)
        
        if simulate_motors:
            self.stepper_alt = simstepper()
            self.stepper_az = simstepper()
        else:
            self.motorkit = MotorKit()
            self.stepper_alt = self.motorkit.stepper2
            self.stepper_az = self.motorkit.stepper1
        
        self.style_alt = stepper.SINGLE
        self.style_az = stepper.SINGLE
        
        if self.style_az == stepper.MICROSTEP:
            self.steps_per_turn_az *= 16
        if self.style_alt == stepper.MICROSTEP:
            self.steps_per_turn_alt *= 16
        
    def __del__(self):
        try:
            self.stepper_alt.release()
        except:
            logging.error("Could not release alt stepper on exit!")
        try:
            self.stepper_az.release()
        except:
            logging.error("Could not release ax stepper on exit!")
        
    def get_alt_az(self):
        _euler_angles = self.bno055.euler
        # We believe the Euler angles are Z, Y, X, with Z up and Y
        # The order of the Euler angles is RPY. P is alt, Y is az. ???
        # Also note that this is problematic if the base is tilted
        _alt_rad_raw = _euler_angles[1]*np.pi/180.
        _az_rad_raw = _euler_angles[2]*np.pi/180.
        
        # Quaternion is in w, x, y, z format. See table 3-30 in datasheet
        _quaternion = self.bno055.quaternion
        # This wants to be in scalar-last format, see https://docs.scipy.org/doc/scipy/reference/generated/scipy.spatial.transform.Rotation.html
        _rotation = Rotation.from_quat([_quaternion[1], _quaternion[2], _quaternion[3], _quaternion[0]])
        # TODO this is where we figure out the actual axes based on Section 3.4 in the datasheet
        # https://cdn-shop.adafruit.com/datasheets/BST_BNO055_DS000_12.pdf
        # Consider a setup with z axis for az and y axis for alt. Then we want z y x, and we will ignore x.
        # Based on the markings on the chip: https://www.adafruit.com/product/4646
        # This may be Y Z X
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

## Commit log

2021-11-06 Add: LED Manager. Also minor bug fixes
    [led_manager.py]
2021-11-06 Add: local changes on RPi with LED manager sketch
2021-11-07 Add: display manager and debug. Added a display manager for the ssd1309, based on luma library. Note that the i2c speed should be increased, or the display won't work. Also, WOW are SMD parts hard, a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
    [display_manager.py, observables.py]
2021-11-07 Bugfix: clean up display library
    [display_manager.py]
2021-12-06 Fix: handle case where PyEphem is not available
    [observables.py]
2021-12-06 Fix: type incompatibility with Python3.6
    [observables.py]
2021-12-09 Display controller and streamlining. 1. Added new display controller that shows name, type, and distance. 2. Updated Observable type to carry type. 3. Cleaned up Observables to use less memory, reduc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
    [display_manager.py, observables.py]
2021-12-11 Assembling end to end SW
2021-12-12 Add: async LED behavior
2021-12-12 Fix: license. This software was developed by Federico in his spare time, using no JPL resources. The license was autocompleted (VS Code synced the licenser params), and is now correctly set to GPLv3
    [led_manager.py, observables.py]
2021-12-27 Electrical design
    [arrow.fzz]
2022-05-04 Fix: logging and better sim tools
    [arrow_controller.py, display_manager.py, visibility_window.py]
2022-05-04 Add: ZMQ interface for LED manager. Also better simulation tools
2022-06-13 Update config: motor direction
2022-06-20 Bugfix and added calibration status
    [trovastelle.py, trovastelle_web.py]
2022-10-29 Fix: process configuration based on common keys. We now accept PUSH requests with a config with extra keys, which will be ignored. Previously, if the configuration file had keys not understood by the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
    [arrow_controller.py, display_manager.py, led_client.py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]
2022-10-30 Fixes: observables list, calibration level, advanced settings. Shows list of observables in the frontend. Resolves #17. Allows user to set calibration level in frontend and backend. Resolves #46. Res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
    [arrow_controller.py, compass.py, trovastelle.py]
2022-10-30 Add: calibration level in base config
2022-10-30 Fix: list of objects is now loaded in main. Previously, the list of objects was loaded separately by the d3-celestial map. Now it is passed in as a prop. Resolves #45
2022-10-31 Manual fetch and push buttons, improved CelestialMap. - Added manual buttons to push and fetch data, so we do not hit the server on every page update. - Celestial map properly removes old information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
    [trovastelle.py, trovastelle_web.py]
2022-10-31 Fix: return target positions in ra-dec. Positions were previously returned in alt-az for the frontend. Resolves #41
    [compass.py, observables.py, trovastelle.py]
2022-12-04 Fix: app creator for WSGI
    [trovastelle_web.py]
2022-12-05 Fix: resolved bug in observables loading. Observables were loaded according to a stale config instead of the most recently received one. Resolves #49 (not a race condition after all).
    [compass.py, trovastelle.py]
2022-12-06 Slow down i2c display updates. Add logging, retries, and a pause to handle a temperamental i2c display interface. Designed to resolve #51. As it turns out, disassembling and reconnecting quick-connec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
    [compass.py, display_manager.py, trovastelle.py]
2022-12-10 Add: frontend config to toggle slow i2c update. Resolves #57. Also fixes status bar at the top when scrolling.
    [compass.py, display_manager.py, trovastelle.py]

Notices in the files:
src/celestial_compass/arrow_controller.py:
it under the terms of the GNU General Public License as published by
